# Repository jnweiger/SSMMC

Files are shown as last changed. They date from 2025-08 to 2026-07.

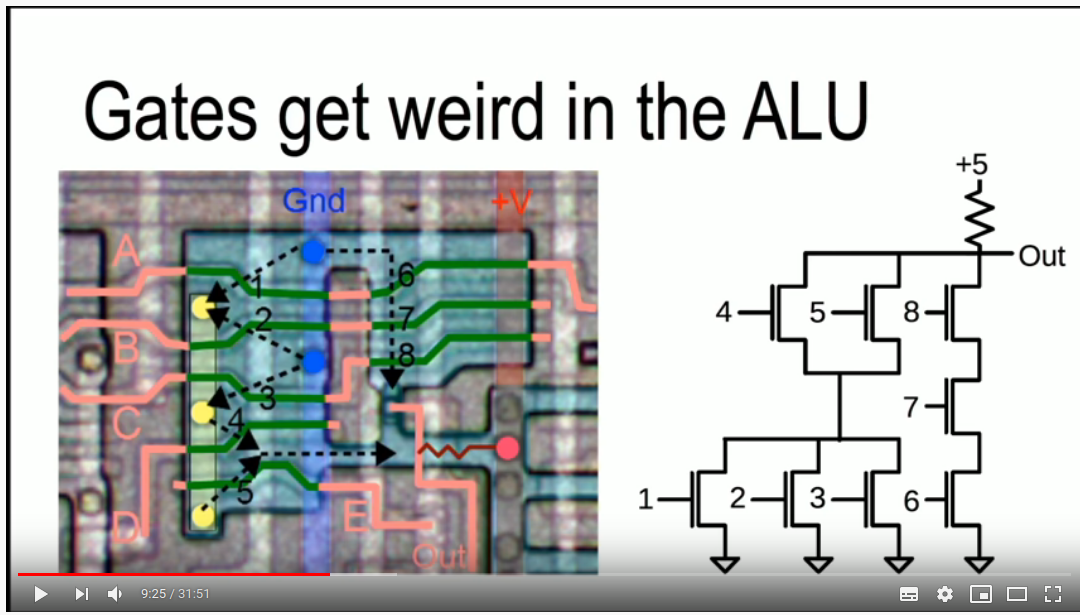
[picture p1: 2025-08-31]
z80/Screenshot from 2020-03-30 22-49-19.png

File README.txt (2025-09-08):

output unit:
We build a binary to unary decoder, and let the marbles roll into an output stack. 
This is the same binary to unary decode we need for loading jumps into the pc stack.

program rom is 10 bits wide. 6 bits for an embeded data word, 4 bits for an opcode. TODO: Is 16 opcodes sufficient?

Program counter:
A stack of marbles. It encodes in unary. Normal operations add one marble to the pc stack, so that the next command
gets addressed. 
"Relative forward jumps" can optionally put n extra marbles in the pc stack.
"Reset PC" drains all marbles from the pc stack.
A backwards consists of a drain, followed by putting in n marbles.

The command decoder senses the height of the pc stack and selects a microcode punch card (or a microcode conveyor belt) based on the binary code found there.

-----

All microcodes reset program counter increment to 1.
All microcodes reset the timer step counter to 0. 
All microcodes program their done flag to fire after a maximum T=n steps.
When a microcode done flag was raised, subsequent time steps move the program counter until all increments are done. 
the program counter advances one memory register, where the next microcode is found.

microcode operations:
X X X 0 0 1	Multibit Add in Register X. Stops after T=6

Multiplier
----

Modeeled after the Leibniz Box with Holes idea.
It needs 3 things.
1) A set of three registers A, B, X of 6 bits each. X needs to have safety rails, to dump bits above 6 and set a mechanical 
   overflow flag, if so.
2) a register copy mechanism: A into X with left shift (0-5). 
3) a register bit walk, that performs "an operation" if the relevant bit of Register B is set.

A moveable platform consists of 6 Gates, that can be switched on or off. The gates sit between a 6 bit latch gate on a power rail and register X.
In T=0, the bits of register A are transfered into open/closed gates of the platform.
In T=1, the latch gate opens for one ball. Where platform gates are open, a marble rolls from the power rail into 
register X
In T=2, the platform moves one bit position to the side.
In T=3,4 until T=11,12 the same actions are repeated. 
(the platform should be built as a conveyor belt, that loops back to the beginning, if possible. Otherwise, we need an extra step 13, that bring the platform back)

----

ITA or Baudot-Murray Punch tapes use 5 bits. With a Letter shift and Figure shift code to extend to effectively 64 code points.
https://en.wikipedia.org/wiki/Baudot_code

Baudot code does not have the digits sequentially (as ASCII or ECMA-1 would have them). We need a complex decoder and encoder for numbers.
(Or we design our own encoding...???...) Compatibility with vintage punch-tape readers and writers would be a good thing, oto. ?

ECMA-1 or DEC-SIXBIT have a much nicer encoding....

We use 6bit internally, to address a register bank of 64 registers.
For educational value and real live relevance we should have 8 bits per word.

Speed classifications
---------------------
Modern computers are speed of light computers. Electrons move accross the wires very fast.
Ancient computers are speed of mechanics computers. Levers, rods and gears can be driven slow or fast, by always several magnitudes slower than the speed of light.
Now, there is also speed of marble computers. At any given slope, the gravity of the earth applies a 
constant drving force on a marble. The speed a marble reaches, can be slowed down by obstacles or other 
elements, but we cannot speed up gravity. A rolling marble has its inherent speed. It cannot "be rolled faster" by cranking the machine faster. This only brings the marbles earlier to the top positions, but letting them roll
just takes its time.

We intentionally build a slow computer.
 - Being mechanical, it cannot win any speed competitions anyway.
 - Whenever there is a decision speed versus simplicity, we go for simplicity. (Minimize part count)
 - Whenever there is a decision speed versus transparency, we go for transparency. (Visible operations)
 - Clock by hand-crank. Primary use is for education. 
 - artificial slowification, e.g. by "you can always add another level of indirection" is to be avoided.
 - Slow down by slowing the clock is for debugging or manual control only.
   The nominal speed (slowness) is measured with the fastest possible clock that still works reliably.

Pushing rods like on the Z1 can be moved quite fast. The Z1 also uses thin
metal sheets to achieve tight packing.  All this makes it not easy for a human
to follow the operations. Especially the flow of information is invisible.
Looking at one long part that is coupled with other parts, it is often not
apparent, what part drives, and what part is driven. Both ends of a long part
move at the same time. The Zuse Z1 does not aim at visualizing its operation.
We do. Marbles make the flow of information visible, as humans can follow their
motion from start to end.

SM3C-Elements
=============

Marbles
-------
Marbles represent electricity and data. When on the power rails and reservoirs, a marble can be though of as an electron. It moves from higher loctions to lower locations, entering logic elements, busses and storage elements. It finally arrives in the dump, to be recycled in the power supply.
Steel, plastic and glass are available.
We need many. Guesstimate:  full RAM module of 64x6 = 384. Having twice or three times as much should be sufficient for a start.

The size and weight of the marbles defines the size of the entire machine. The weight influences the choice of mechanisms.
One of the largest component of the machine is probably the memory.64 cells with 20mm per cell require a length of 1.24m.

The machine building blocks should not exceed 55cm x 36cm, so that they fit in standard Eurobox containers.
The memory unity needs to be split into 3x 55cm or 4x 36cm in this case.

https://www.amazon.de/Warenfux24-RPN-Glasmurmeln-Glaskugeln-Dekoration/dp/B079W3FMHV/
800 glass marbles cost ca. 20 EUR, ca 5gr each.
The smallest acceptable size is 15mm, the largest acceptable size is 17mm.

https://www.amazon.de/Umarex-Stahlrundkugeln-5000-St%C3%BCck-BB%60s/dp/B004PH88F8/
5000 steel balls 4.5mm diam cost ca 17 EUR.
Not stainless.

https://www.amazon.de/Ultrasport-Unisex-Erwachsene-Softair-Munition-0-20/dp/B019H12VPE/
4000 PLA balls 6mm diam, cost ca 13 EUR. 0.25gr (!) each.
Lightweighted. Detecting a ball cannot be done by weight. Only by poke.

https://www.amazon.de/Stahlrundkugeln-Edelstahl-St%C3%BCck-Steinschleuder-Zwille/dp/B00DV5VU3W/
500 stainless(?) steel balls, 8mm diam, cost 11 EUR + 4.90 EUR

https://www.amazon.de/dp/B07MFWRSTR/
1000 nickel-steel balls, 8mm diam, cost 21 EUR, 2.0gr each.

https://www.amazon.de/-/en/Original-Shoot-Club-Slingshot-Ammunition-Catapult/dp/B08VF8TGJZ/
	1000 steel balls, 8mm, 18 EUR + 5.89 EUR

https://www.amazon.de/Sector-71-Stahlkugeln-Schleudern-Verschiedene/dp/B01I4ZDUP4/
200 carbon-steel, 10mm diam, cost 12 EUR, 4gr each

https://www.amazon.de/Muzzler-Premium-Stahlkugeln-Schleudern-Katapult/dp/B01N06GKMR
400 carbon-steel, 10mm diam, cost 18 EUR, 4gr each

https://www.amazon.de/Vancool-Professional-Kunststoff-Slingshots-Plastikperlen/dp/B073XH9R3D
500 plastic, 10mm diam, cost 14 EUR, ca 0.6gr each

https://www.amazon.de/g8ds-Marken-Schleudermunition-Stahlkugeln-Schleuder-Munition/dp/B07GS91Y3B
500 steel balls, 12mm, cost 25 EUR

https://www.amazon.de/12-mm-Kohlenstoffstahlkugeln-umweltfreundlich-Maschinenbau-Heimwerker-Kugellager/dp/B0DQCKZQLS
200 steel balls, 12mm, 1.4kg, cost 12 EUR

https://www.amazon.de/sourcing-map-Lagerkugeln-Chromstahl-Pr%C3%A4zisionskugeln/dp/B0822LMMM6
50 steel balls, 12mm, Chromstahl G10, 17.30 EUR

https://www.ebay.de/itm/335435976697?var=544846175789
100 steel balls, 12mm, Edelstahl rostfrei G100, 20 EUR

############################################################################
https://www.ebay.de/itm/396583747630
127 stück, 0.95 kg, 12mm, Chromstahl C15, 9 EUR + 5 EUR

https://www.amazon.de/g8ds-Marken-Schleudermunition-Stahlkugeln-Schleuder-Munition/dp/B07GSG2P8Y
200 steel balls, 16mm, cost 11 EUR.

https://www.amazon.de/g8ds-Marken-Schleudermunition-Stahlkugeln-Schleuder-Munition/dp/B07GSBQWFG
500 steel balls, 16mm, cost 27 EUR.

16mm is affordable. Steel or glass. There is no need for plastic or clay.

12mm steel is probably better: 500 balls 12mm weigh ca 3.5 kg,

Power supply
------------
An elevator mechanisms that shovels marbles from the dump to the start of the power rail tree. The main crank drives the elevator. Additional elevators should be easy to add. During start-up the elevators have to shovel up enough marbles to fill all reservoirs to at least their low-water marks. (Elevators can pause, when all rails dump marbles.)

Elevators have a define entry diameter of 17mm. Anything larger is dropped into the drain.
Elevators have a defined exit diameter of 15mm. Anything smaller than that is dropped into drain.

Power rails
-----------
A "never ending" supply of new marbles. It is mechanically higher than all other element so that gravity plays the role of 
voltage. Each logic element has a reservoir (think of "capacitor") of marbles connected to the power rails. Each marble rolling on a power rail will enter the first non-full reservoir. If all reservoirs are full, excessive marbles are dumped.
Each reservoir has a low water flag. If less marbles are in the reservoir, than possibly needed in one clock cycle, a flag is shown.

The power rails start with a binary distribution tree to distribute marbles into a set of "parallel" power rails. This allow easier 2 dimensional distribution. The reservoirs of logic elements with high consumption can be connected to two or more power rails.

Dump
----
A "ground plane" under the machine that collects excess marbles. From the lowest point of the dump, marbles are fed to the power supply or to the drain bucket (if one is placed under the drain next to the lowest point).
A large piece of cloth serves as a safety net. It also covers the marble drain, unless pushed back by a bucket.
No marble should ever drop to the floor.
Near the high end, the dump has a marble loading ramp, where humans can dump buckets of new marbles. Any spilled marbles should go to 
the safety net.

Glossary
--------

coupled: Mechanically coupled by levers, rods or other gear. No marbles are involved. This has immediate effect.

connected: Marble rails are connected by switches. Marbles need to pass through to cause an effect further down.

Marbles: We rather use high precision steel balls instead of glass marbles. They don't break and run smoother.

derail: a mechanical obstacle blocks a rail (one bit of a bus) and causes any oncoming marbles to be dumped, or stored elsewhere.

SM3C-Clock
==========
Clock distribution is a mecanical coupled grid, that is moved in small circles,
so that in every position of the grid the same circular movement can be
obtained. We subdivide clock cycles in four phases: I) down, II) right, III) up, IV) left.
(Z1 calls them north, south, east, and west)

The main hand crank takes two, four, or eight revolutions to complete one clock
cycle, depending on the needs of the power supply.  Side effect of the speed
reduction: People usually want to crank as fast as they can. The reduction gear
helps to keep the clock reasonably slow. The name already says "slow motion", right?

For manual cranking, a reduction of four is best. This allows to listen for marble movement duing rotation.
The time elevator always deliver one timing marble per clock phase.

Rule: You are only allowed to crank the next revolution, after you heared the timing gong.
The timing marble runs through a certain length of rail, to delay it a bit more than the longest possible operation.
The timing marble finally dumps onto a bell, to sound the gong. (There may be noises after the gong, coming from the dump)

For electric cranking, a watchdog timer starts, when the cranking starts.
 The watchdog is reset, and a short delay is started when the timing marble hits the gong.
 After the short delay is up, the motor cranks the next revolution.
 If the watchdog expires, the motor starts making beep noises. As soon as the gong is hit, normal operation resumes.

SM3C-Output
===========
Output devices can be very slow. E.g. Unary encoding, and using weigths.
Very nice would be a 3x5 Font represented by marbles.

SM3C-RAM
========

Memory is going to be mechanically large. We build it in banks, so that it is extendible.
Each bank has 16 words, its own 4 bit address decoder, and its own data bus.

To form a memory unit out of multiple banks, we arrange identical bank ontop of each other.
The memory data bus starts with a bank decoder. A two or 3 bit decoder sufficiently demontrates the idea.
Only one bank (or none) is connected to the data bus at any given time.
Bank position 0 remains empty, so that our address space has a "zero page".

Address decoder
---------------
The address register is split into 4 lower bits and 2 (or 3) upper bits.
Each bank has its address decoder switches coupled to the 4 lower bits.
The upper bits of the address register are coupled to two bank selector units:
One address selector and one data bus selector. 

Each clock cycle at I), the addess selector receives one marble from the
power grid and sends it to one of the connected bank address decoders.

Each clock cycle at III), the data bus selector receives a full word of 6 marbles from the power grid 
and sends it to one of the connected banks.

Both, address selector and data bus selector should be built vertically, to gain speed.

If no memory operation is needed, bank 0 is selected and the marbles from both selectors are 
are dumped into the sink. 

Read
----

By the start of II), one of the banks has a selected cell. A marble has arrived through the address decoder, and couples the cell to the copy mechanism.
At II), the copy mechanism probes the bits of the cell and derails the data bus, where an empty bit is found.
At III) marbles run down the data bus, and at beginning of IV) the data output register has a copy of the selected cell.
During IV) the cell selecting marble is dumped and the copy mechanism resets.

Erase
-----
The cell selecting marble couples the dumper mechanism. During II), the marbles are dumped from the cell.
Override switches derail the data bus selector.
At the beginning of III) the cell dumper mechanism is reset.
During III) data bus marbles are dumped in the selector.
During IV) the cell selecting marble is dumped and the mechanisms resets.
No marbles arrive at the output register.

Erase is actually the same as a write with an empty data input register.
That is why the cell dumper needs to reset early :-)

Write
-----
The cell selecting marble couples the dumper mechanism. During II), the marbles are dumped from the cell.
The override switches to derails the data bus selector are coupled to a data input register.
The override mechanism probes the bits of the input register and derails the bus where an empty bit is fouund.
At the beginning of III) the cell dumper mechanism is reset.
During III) data bus marbles transport the bit pattern of the input register. The data bus is derailed at the 
selected cell so that marbles from the bus end in the memory cell.
During IV) the cell selecting marble is dumped and the mechanisms resets.
No marbles arrive at the output register.

Adder
-----

Register B is added to Register A inplace.
Easy case: Register B contains the value 1:
 The incoming marble triggers the probe mechanism of the bit position where it comes in.
 If the bit is 0, the new marble is placed in that position. Done.
 If the bit is 1, the old marble is dumped, and the new marble is transfered left, to the next bit position.
	Timing problem. Multiple marbles are incoming roughly simulaneously. If
	a marble gets trandfered left, then one rail has two marbles.  There is
	no defined distance between them, while in motion. The mechanics cannot safely
	distingusih two marbles from one.
 Aternative idea: 
	Serial (ripple carry) adder. The second marble bumps into the first,
	and thus stops in the probe position. A mechanical probe comb detects marbles
	in these position and initiate transfers and dumps. All dumps are executed in
	parallel, but the transfers are split into multiple steps. 
	1) "carry" marble while the probe moves downwards,
	2) let the marble roll into the rail to the left when the probe moves upwards and thus gives way.
	Repeat the probe movement n-2 times on an n-bit adder, to allow a
	controlled worst case transfer from bit position 0 to n-1.
  Repeat.
General case:
 For an 8-bit word, we need 8 clock cycles. In each clock cycle:
   If there is no marble coming in I) at a certain bit positon, the probe mechanism reads a 0 during II), 
   and prepares to insert the new marble during III) nothing happens, as there is no marble.
   If there is a marble coming in during I), the probe mechanism does an actual probe during II) 
     If that was a 0, the new marble is inserted at the current bit position III), probe mechanism resets during IV).
     Else, if that was a 1, the old marble is lifted from its position and the new marble is transfered one position left during III).  
       The lifted marble is dumped and the probe mechanism resets during IV).
  Marbles overflowing to the left of the highest bit are dumped.

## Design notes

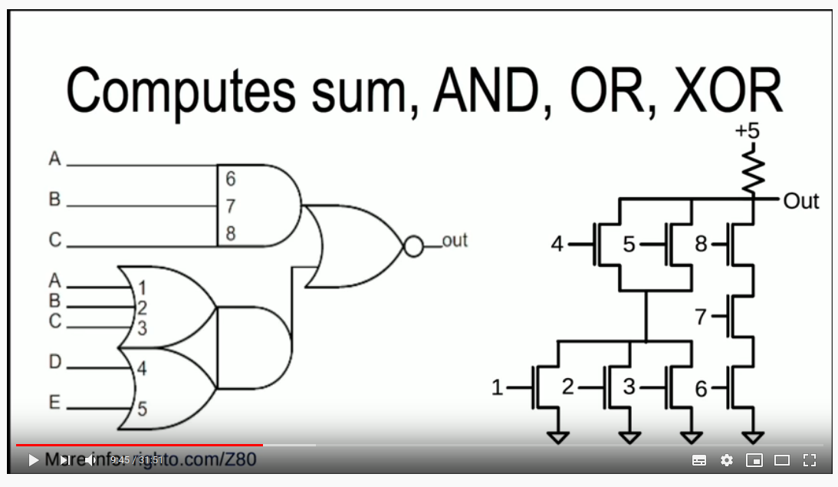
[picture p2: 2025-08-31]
z80/Screenshot from 2020-03-30 22-50-21.png

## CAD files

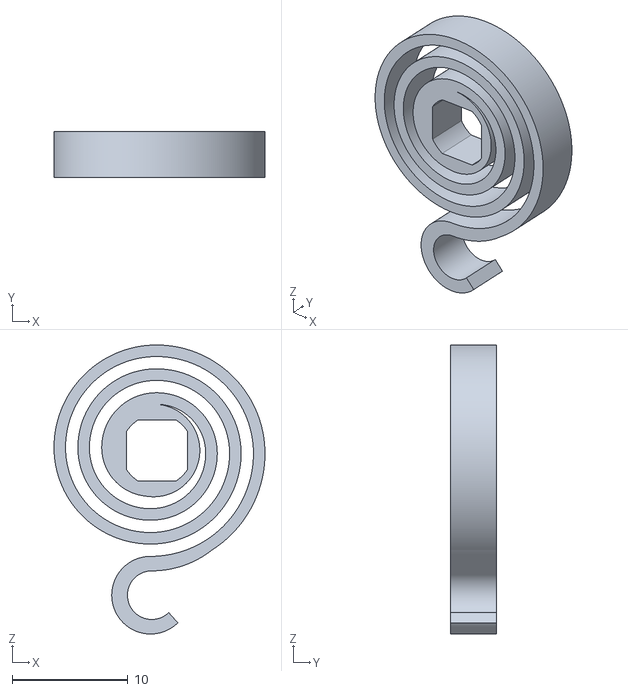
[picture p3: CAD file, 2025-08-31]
adder-test/input/button-array-SpringsMainSpring_4x1mm.stl
18.2 x 4.00 x 25.0

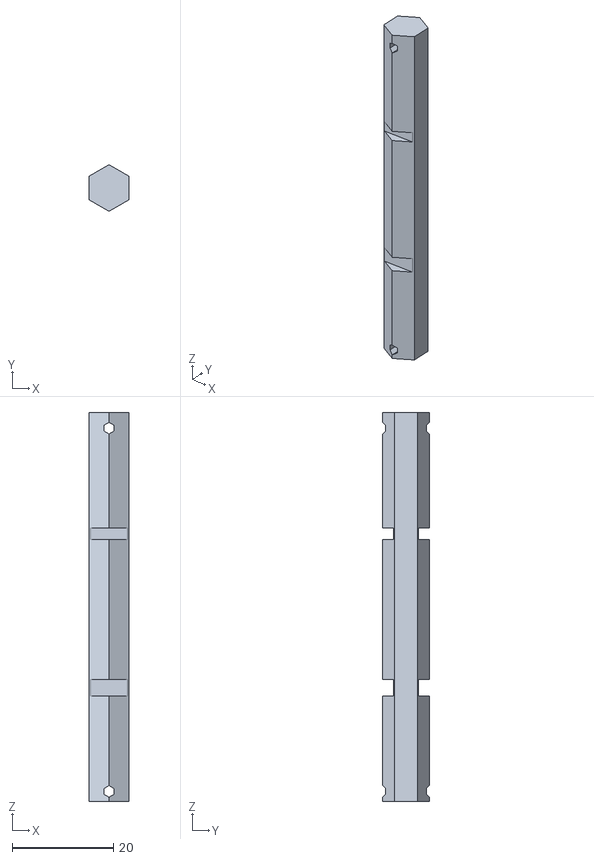
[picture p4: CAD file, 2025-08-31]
adder-test/input/button-array-StaticsMainPost.stl
8.00 x 9.24 x 77.0

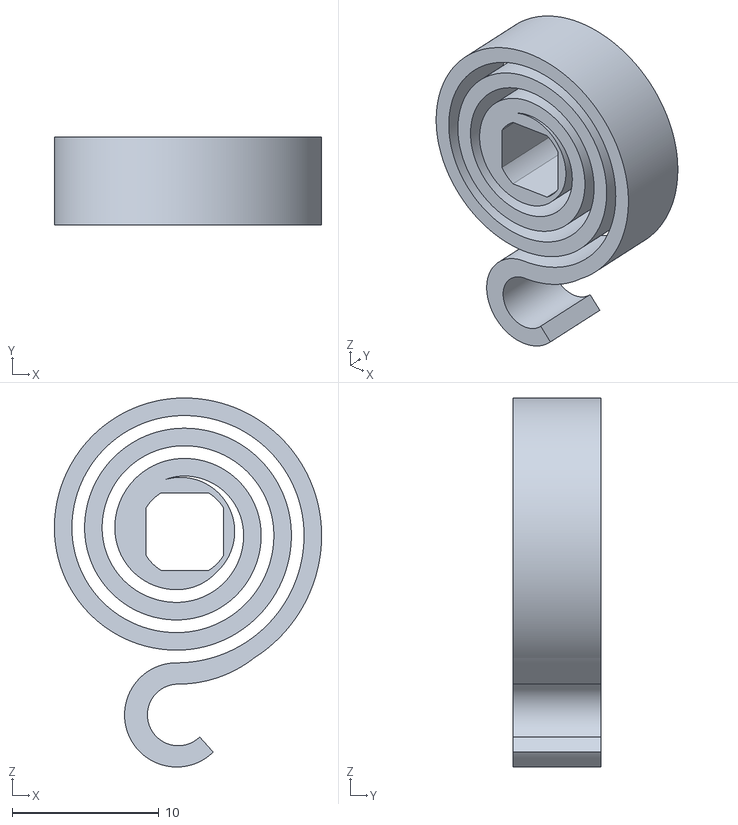
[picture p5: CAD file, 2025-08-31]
adder-test/input/button-array-MainSpring.stl
18.2 x 6.00 x 25.2

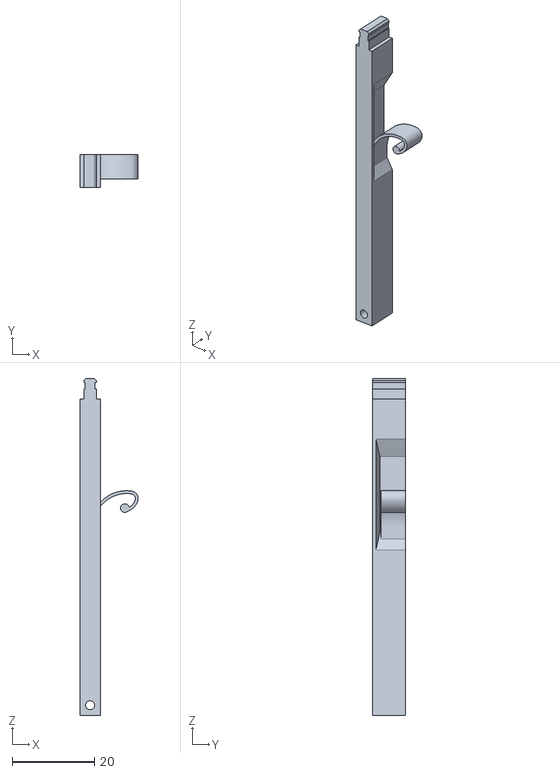
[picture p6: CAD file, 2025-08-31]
adder-test/input/button-array-spring-postsspring-post-ones.stl
14.2 x 8.00 x 82.0

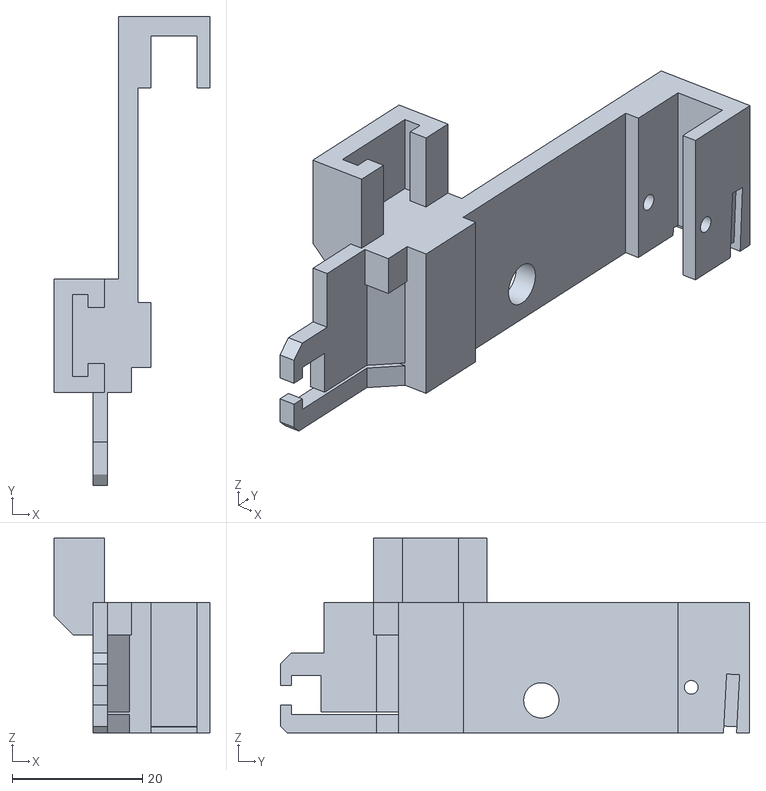
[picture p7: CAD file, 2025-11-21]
adder/12mm/12mm-Mount.stl
23.9 x 71.9 x 29.9

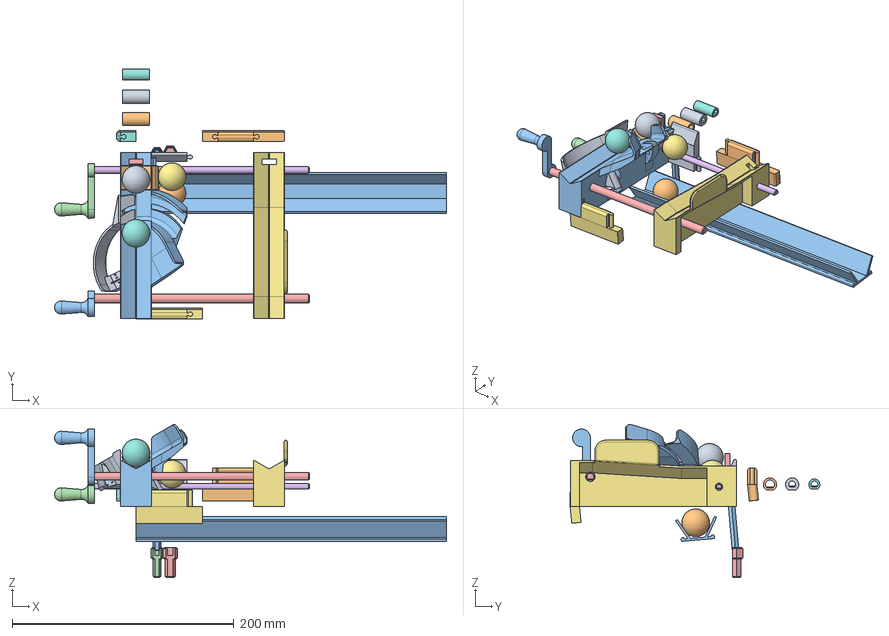
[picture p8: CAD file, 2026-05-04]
adder/25mm/adder25mm.FCStd
353.5 x 225.2 x 138.3 mm
Carry
Rocker
V-Groove
Blocker-sprocket
Blocker 31mm
Carry-Drive-Link
rcon-raised
rcon-raised-cut
rcon-simple
rcon-raised-last
Post6mm
Post6mmExt20mm
Post8mmExt20mm
V-Groove-last
Coupler-6-6mm
Coupler-8-6mm
Coupler-8-8mm
Carry-Crank
Blocker-Crank
Carry-Drive-Shaft
Blocker-Drive-Shaft
DumpRail

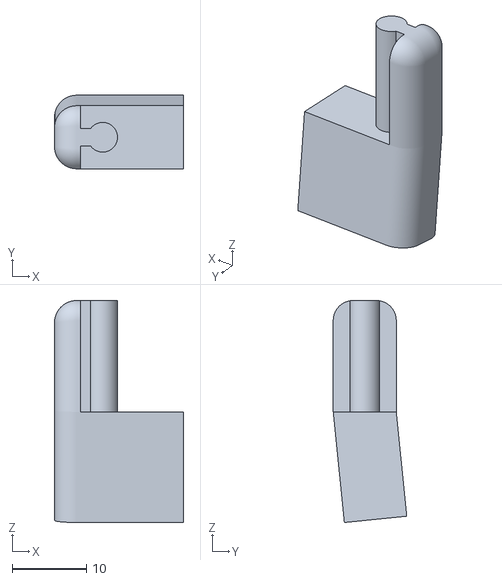
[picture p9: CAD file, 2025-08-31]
adder/25mm/stl/v-test-Connectorsrcon-raised-cut.stl
17.4 x 9.92 x 29.9

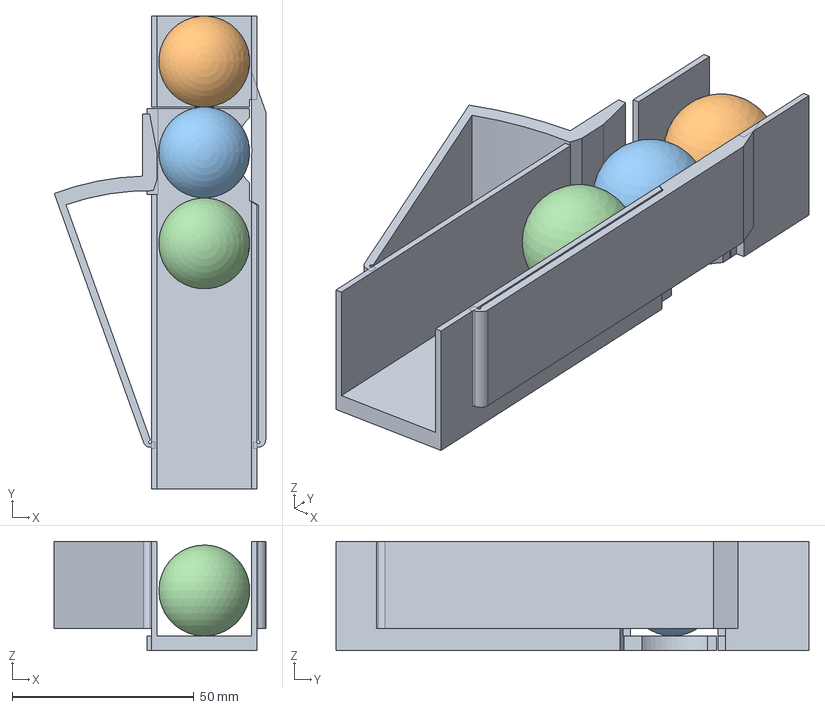
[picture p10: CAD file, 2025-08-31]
adder/25mm/test/Adder-test.FCStd
58.1 x 130.0 x 30.0 mm

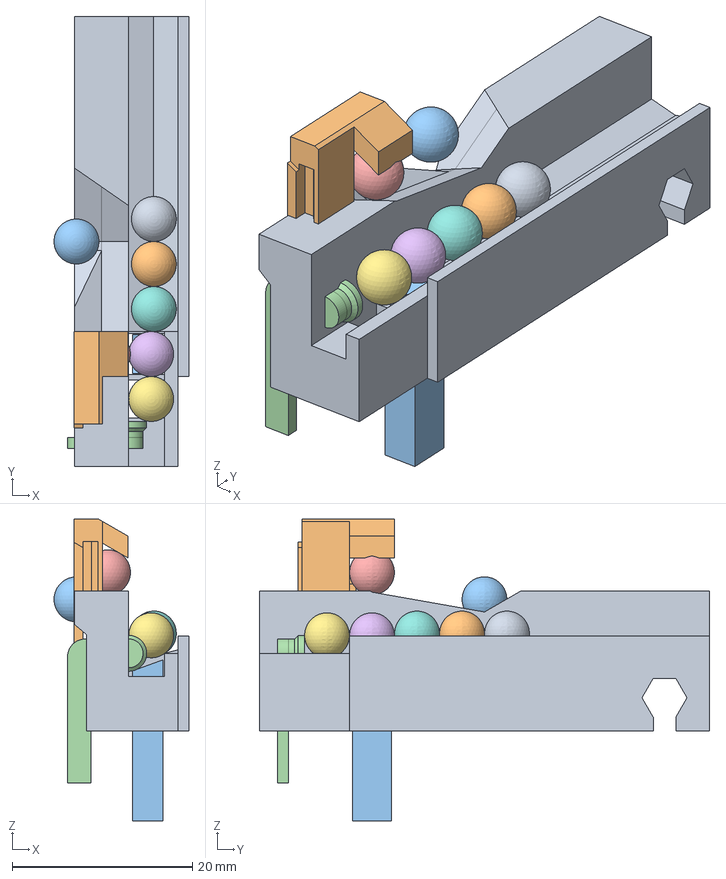
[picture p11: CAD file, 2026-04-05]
adder/5mm/adder5mm.FCStd
15.0 x 50.0 x 33.5 mm
DiscardLift
CarryLift
Stopper

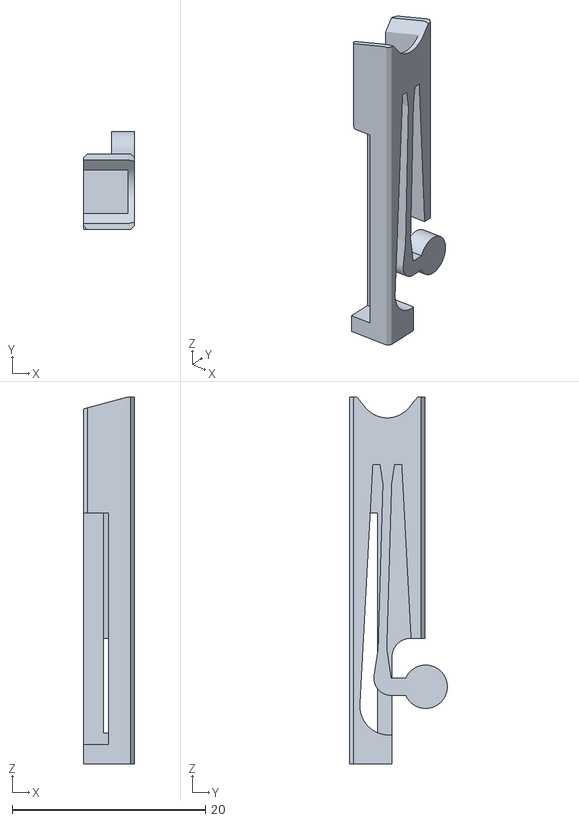
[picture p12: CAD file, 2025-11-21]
adder/8mm/8mm-Piston.stl
5.30 x 10.1 x 38.0

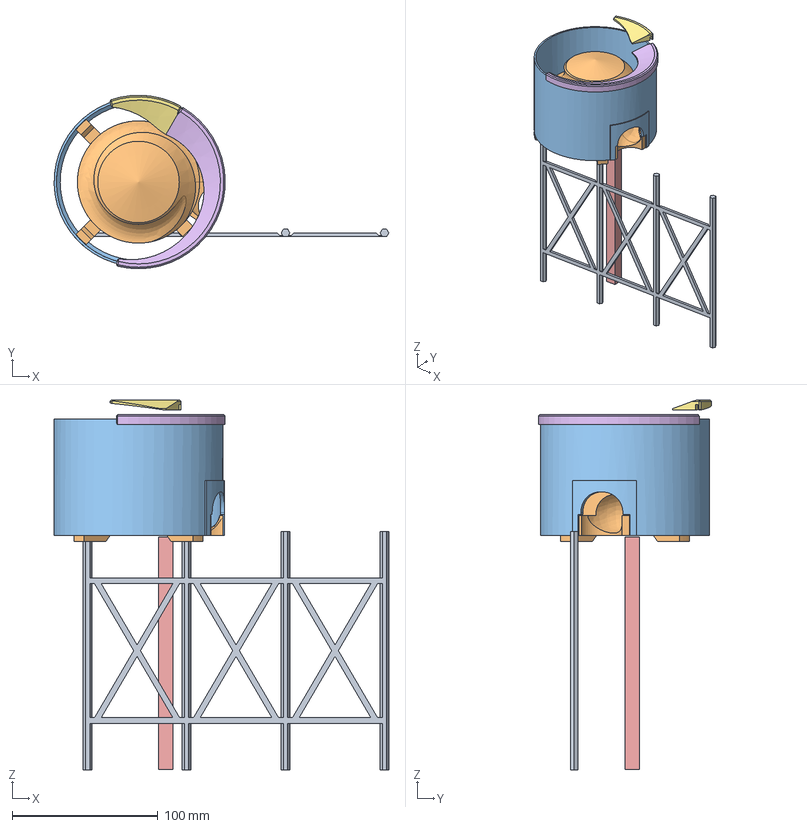
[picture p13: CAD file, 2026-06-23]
feeder/Feeder.FCStd
230.0 x 119.2 x 254.2 mm
Legs
SpiralTower
TowerWall
Kugel
Quader
Scythe
PreScythe

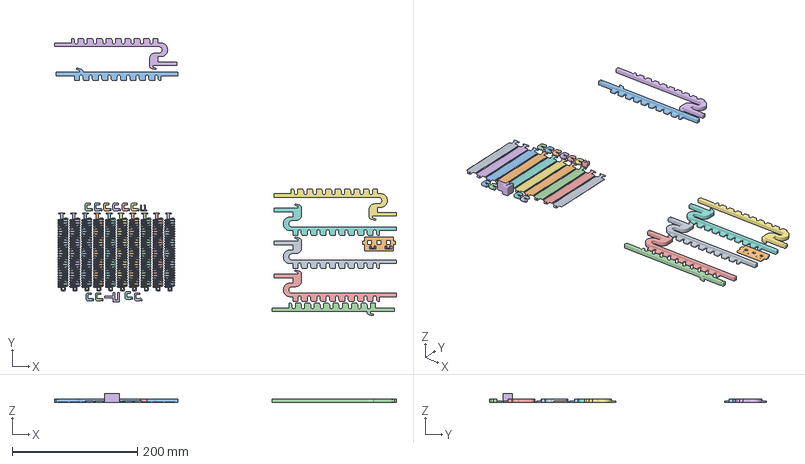
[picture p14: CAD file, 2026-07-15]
input/3mf/throwers-springs.3mf
546.1 x 443.0 x 15.0 mm
thrower-LongSpring.stl
thrower-Or-Gate-Rod.stl
thrower-Or-Gate-Rod-lower.stl
thrower-comb001.stl
thrower-SpringAdapter.stl
thrower-Frame9stop.stl
thrower-Frame60stop.stl

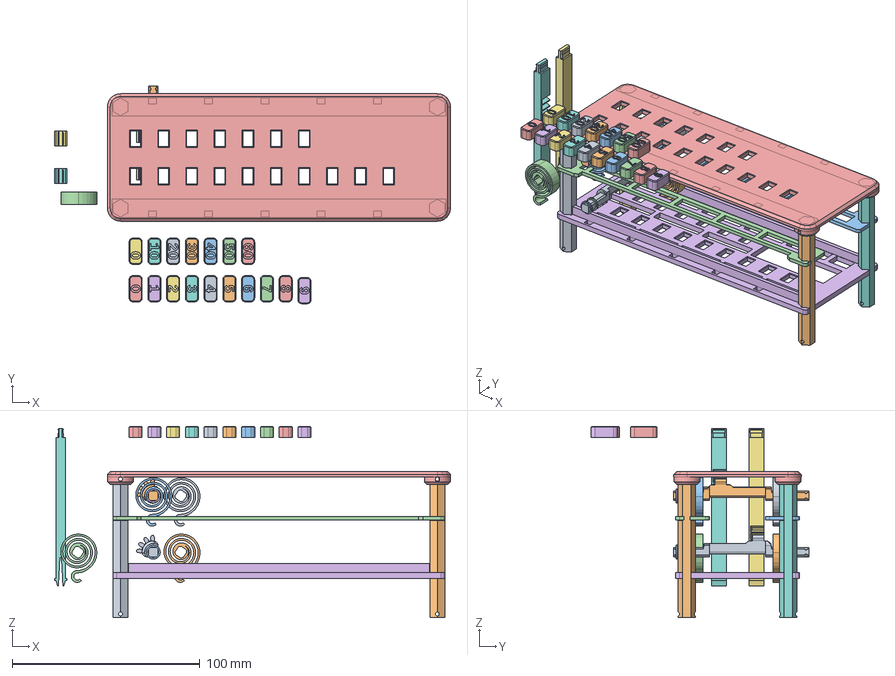
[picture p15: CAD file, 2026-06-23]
input/button-array.FCStd
211.2 x 116.0 x 102.1 mm
shaft-gear-tens
shaft-gear-ones
ShaftRing
ShaftRing001
ShaftRing002
ShaftRing003
gear-post-tens
gear-post-ones
MainSpring003
MainSpring002
MainSpring001
MainSpring_6.6x1mm
top
bot
MainPost
MainPost001
MainPost002
MainPost003
Ladder-tens
Ladder-ones
Cap000
Cap001
Cap002
Cap003
Cap004
Cap005
Cap006
Cap007
Cap008
Cap009
Cap_00
Cap_10
Cap_20
Cap_30
Cap_40
Cap_50
Cap_60

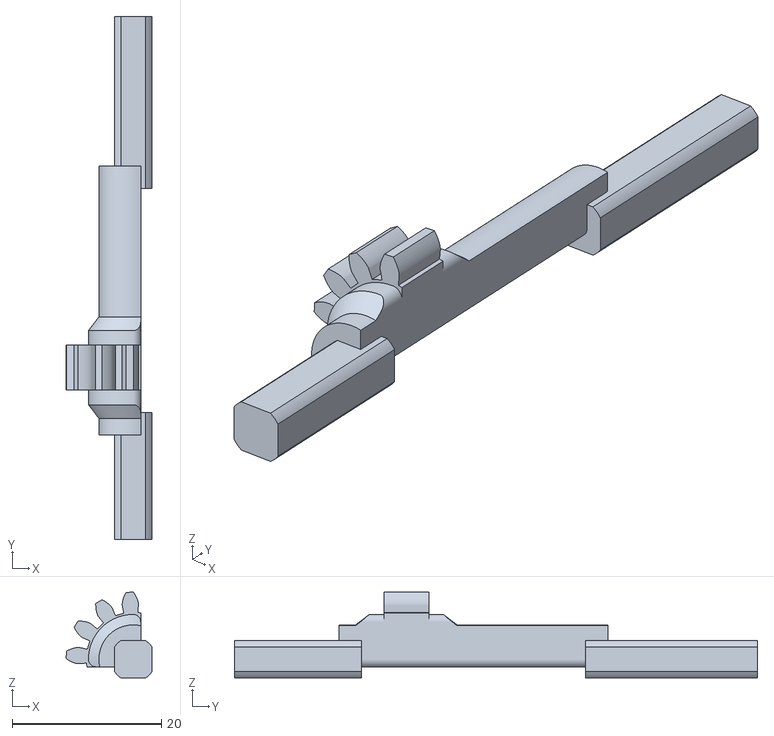
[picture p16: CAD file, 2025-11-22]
input/stl/button-array-Shaftsshaft-gear-ones.stl
11.5 x 70.0 x 11.5

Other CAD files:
Labels/labels-Four.stl
marble-elevator-spiral.FCStd
output/3to8-chain/chain.FCStd
output/3to8-gear/3to8.FCStd
Labels/labels-Board1.stl
Labels/labels-Board16.stl
Labels/labels-Board2.stl
Labels/labels-Board32.stl
Labels/labels-Board4.stl
Labels/labels-Board8.stl
Labels/labels-Connector.stl
Labels/labels-Eight.stl
Labels/labels-One.stl
Labels/labels-Rail.stl
Labels/labels-Six.stl
Labels/labels-Three.stl
Labels/labels-Two.stl
Labels/labels.3mf
Labels/labels.FCStd
adder-test/input/button-array-ButtonsCap000.stl
adder-test/input/button-array-ButtonsCap001.stl
adder-test/input/button-array-ButtonsCap002.stl
adder-test/input/button-array-ButtonsCap003.stl
adder-test/input/button-array-ButtonsCap004.stl
adder-test/input/button-array-ButtonsCap005.stl
adder-test/input/button-array-ButtonsCap006.stl
adder-test/input/button-array-ButtonsCap007.stl
adder-test/input/button-array-ButtonsCap008.stl
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

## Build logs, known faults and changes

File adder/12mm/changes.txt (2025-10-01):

Kurbel antrieb: 
bei jeder umdrehung ein nocken, der den finishpusher herauszieht.
wenn eine kugel fällt, wird der finishpusher vom sich hebenden gate zurückgeschoben
-> falls der finishpusher noch vorne ist, wird in der nächsten Umdrehung (!) ja, wir haben zeit. der stopper gesenkt.

Oder fest 8 Umdrehungen piston, ein Nocken, der den Stopper auf macht.

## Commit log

2025-08-31 A machanical computer, functional an simple.
    Unfinished draft.
    adder-test is still the main folder, where development happens.
    [Adder-test-Body.3mf, Adder-test-Body.stl, Adder-test.FCStd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]
2025-09-03 a testrail with a large swing. It probably collides with its right neighbor. Sigh.
    [TestRail-large-swing.FCStd]
2025-09-04 TestRail-gate-piston.FCStd looks promising
    [TestRail-gate-piston.FCStd, TestRail-large-swing.FCStd]
2025-09-04 Marble raises the gate nicely, but dropping the marble through the gate might become an issue.
    [TestRail-gate-piston.FCStd]
2025-09-08 Added the bridge.
    [TestRail-gate-piston.FCStd]
2025-09-11 second attempt.
    [TestRail-gate-piston.FCStd, TestRail-gate-piston2.FCStd]
2025-09-14 TestRail2 works fine.
    [TestRail-gate-piston2.FCStd]
2025-09-22 Connecting Rod added to piston
    [TestRail-gate-piston.FCStd, TestRail-gate-piston2.FCStd, TestRail-large-swing.FCStd]
2025-09-22 added excenter, mount, shaft.
    [TestRail-gate-piston2.FCStd, TestRail2.3mf]
2025-09-24 added stackable crank...
    [TestRail-gate-piston2.FCStd, TestRail.3mf, TestRail.FCStd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]
2025-09-25 adjusted crank pressfit with backcut, enlarged wall mount hole for crank a bit.
    [TestRail.3mf, TestRail.FCStd]
2025-09-25 revamping 12mm into 8.4mm version. WIP.
    [TestRail8mm.FCStd]
2025-09-26 8mm rail and gate done. piston WIP
    [TestRail8mm.FCStd]
2025-09-30 renamed things, floor added.
    [TestRail.FCStd, TestRail12mm.FCStd, TestRail8mm.FCStd]
2025-09-30 ball eject needs more room, stopper mechanics cannot fit under the rail.
    [TestRail12mm.FCStd, TestRail8mm.FCStd]
2025-10-01 Added experimental WedgeStopper to 12mm.
    [TestRail12mm.FCStd]
2025-10-01 12mm version mit WedgeStopper.
    [TestRail12mm.FCStd]
2025-10-02 8mm chute enlarged. Balls can now be ejected.
    [TestRail8mm.FCStd]
2025-10-03 synced and bugfixed 8mm and 12mm -- now we need a test-print to find remaining bugs.
    [TestRail12mm.FCStd, TestRail8mm.FCStd]
2025-10-23 refined, probably working. In PLA, the gate is quite loose, the dovetail is very loose and needs some material to stick into.
    [8mm.3mf, Adder8mm.FCStd, TestRail8mm.FCStd]
2025-10-23 Added now with collector rails.
    [8mm.3mf, Adder8mm.FCStd]
2025-10-25 updated 3mf file with final working designs.
    [8mm.3mf]
2025-10-26 extended back
    [8mm.3mf, Adder8mm.FCStd]
2025-10-29 Result collector on legs. Hook for crank mechanics at Front.
    [8mm.3mf, Adder8mm.FCStd]
2025-11-06 handcrank added
    [Adder8mm.FCStd]
2025-11-21 moved adder-test into github. Now it is public!()
    [12mm-FinishPusher.stl, 12mm-Gate.stl, 12mm-Mount.stl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]
2025-11-22 shaft-gear-ones done.
    [button-array-Shaftsshaft-gear-ones.stl, button-array-Shaftsshaft-gear-tens.stl, button-array-spring-postsgear-post-ones.stl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]
2025-12-07 revamped spring posts to geared posts.
    [button-array.FCStd]
2025-12-11 adjusted geared posts
    [button-array.FCStd, thrower.FCStd]
2026-03-11 three different output drafts, side by side: linkage, bin2dec, 8x8
    [comp-FRame.3mf, comp-Probe4.3mf, comp-ProbeClip.3mf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]
2026-03-16 gear and slider mechanics coming up...
    [3to8.FCStd]
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2026-04-01 simple macros to give me some basic kinetics.
    [sketch-path-move.FCStd]
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2026-04-02 replaced button group with combobox, to prevent accidential toggling.
    [sketch-path-move.FCStd]
2026-04-02 combobox has a width to make it look nicer
    [sketch-path-move.FCStd]
2026-04-05 adder-test/v-test is now official for 25mm balls.
    [12mm-FinishPusher.stl, 12mm-Gate.stl, 12mm-Mount.stl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]
2026-04-05 folders 12mm 25mm 5mm 8mm all next to each other...
    [Adder-test-Body.3mf, Adder-test-Body.stl, Adder-test.FCStd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]
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2026-04-05 created numbers drum directly from inkscape into prusaslicer, without going through freecad.
    [0-63-coolv-cond-19-p.stl, Number-Drum.3mf, differential.FCStd]
2026-04-09 Number-Drum2.3mf worked nicely, last nigth The print was possible in two files. Black numerals first, only on layer. Second print in white went smooth, even after probing the bed with the numerals on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
    [DrumBox.FCStd, Number-Drum2.3mf]
2026-04-09 added more old unpractical ideas...
    [3to8.FCStd, chain.FCStd]
2026-04-12 crank added, exhaust slider started.
    [3to8.FCStd, crank-Bell.stl, crank-InCrank.stl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]
2026-04-12 schalter 1, 2, 4 done
    [3to8.FCStd]
2026-04-13 Linked crank and DrumBox into 3to8.FCStd We don't really need assembly to assemble Parts in a drawing. Links can do that too.
    [3to8.FCStd, DrumBox.FCStd, crank.FCStd]
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2026-04-14 linked 1-32 labels into 3to8
    [1-32-coolv-Labels-white-labels.stl, 1-32-coolv-Labels.3mf, 1-32-coolv-Labels.FCStd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]
2026-04-20 fine tuning of KugelStop.
    [1-32-coolv-Labels.3mf, 3to8-KugelStop.stl, 3to8-Kugelbox.stl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]
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2026-04-23 Crazy, claude.ai just confirmed, my planetary gear really performes an elliptic curve.
    [3to8.FCStd]
2026-04-24 grid open and close hooks added
    [3to8.FCStd, crank-Bell.stl, crank-InCrank.stl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]
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2026-04-25 inpit slider without collision at bell.
    [3to8.FCStd]
2026-04-26 summators adjusted. they barely fit. sigh.
    [3to8.FCStd]
2026-04-26 lower notch started k
    [3to8.FCStd]
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2026-04-29 sliding window and rod done.
    [3to8.FCStd]
2026-04-29 All parts done. Really?
    [3to8.FCStd, DrumUnit.3mf, schalter.3mf]
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2026-04-30 added more variants of highnotch
    [3to8.FCStd]
2026-05-04 added a simple funnel for feeding balls.
    [3to8.FCStd, Feeder.FCStd, adder25mm.FCStd]
2026-05-04 feeder legs need some experiments..
    [Feeder.FCStd]
2026-05-04 improved stability of funnel legs
    [Feeder.FCStd]
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2026-05-11 Feeder SpiralTower (probably) done.
    [Feeder.FCStd]
2026-05-12 feeder spiral tower dine.
    [Feeder.FCStd]
2026-06-23 wider and slightly larger springs for button array
    [Feeder.FCStd, button-array.FCStd]
